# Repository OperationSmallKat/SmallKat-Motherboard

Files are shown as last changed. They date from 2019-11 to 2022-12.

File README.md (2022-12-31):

# Esp32-S3 Motherboard

## Pins
|Pin|Use|
|---|---|
| 0| Boot|
| 1| Servo 15|
| 2| Servo 14|
| 3| Servo 13|
| 4| Servo 12|
| 5| Fuse 4 ADC|
| 6| Fuse 1 ADC|
| 7| Servo 0|
| 8| Servo 1|
| 9| Servo 2|
| 10| Servo 3|
| 11| Fuse 2 ADC|
| 12| Servo 4|
| 13| Servo 5|
| 14| Servo 6|
| 15| 6V ADC|
| 16| Batt Voltage ADC|
| 17| Fuse 3 ADC|
| 18| Fuse 5 ADC|
| 19| USB -|
| 20| USB +|
| 21| Servo 7|
| 26| AD Servo 1|
| 33| AD Servo 3|
| 34| AD Servo 4|
| 35| Batt Serial TX|
| 36| Heart Beat LED|
| 37| Servo 8|
| 38| Servo 9|
| 39| Servo 10|
| 40| Servo 11|
| 41| SDA|
| 42| SCL|
| 43| TX|
| 44| RX|
| 45| |
| 46| |
| 47| AD Servo 2|
| 48| Batt Serial RX|

## I2C

  * i2c (SCL 42, SDA 41) - BNO055

## Serial 
  * Serial 0: Tx 43, Rx 44
  * Serial 1: Tx 35, Rx 48

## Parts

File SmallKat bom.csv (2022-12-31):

Comment | Designator | Footprint | Num | LCSC
BNO085 | AC1 | BNO085:BNO085 | 1 |  | 18.5 | 18.5
10pF | C15,C16 | Capacitor_SMD:C_0402_1005Metric | 2 | C313080 | 0.0009 | 0.0018
22uF | C17 | Capacitor_SMD:C_0805_2012Metric | 1 | C602037 | 0.0239 | 0.0239
0.1uF | C3,C12,C14,C18,C22,C23 | Capacitor_SMD:C_0402_1005Metric | 6 | C359190 | 0.0008 | 0.0048
2.2uF | C2,C5 | Capacitor_SMD:C_0805_2012Metric | 2 | C2176762 | 0.0076 | 0.0152
1000pF | C24 | Capacitor_SMD:C_0402_1005Metric | 1 | C696907 | 0.0006 | 0.0006
100pF | C25 | Capacitor_SMD:C_0402_1005Metric | 1 | C5142577 | 0.0007 | 0.0007
10nF | C26 | Capacitor_SMD:C_0402_1005Metric | 1 | C115654 | 0.0007 | 0.0007
1uF | C27,C36 | Capacitor_SMD:C_0402_1005Metric | 2 | C5137499 | 0.0021 | 0.0042
4.7uF | C28 | Capacitor_SMD:C_0402_1005Metric | 1 | C255498 | 0.0148 | 0.0148
470nF | C29 | Capacitor_SMD:C_0402_1005Metric | 1 | C2887019 | 0.0026 | 0.0026
10uF | C30,C32 | Capacitor_SMD:C_1206_3216Metric | 2 | C2174589 | 0.0183 | 0.0366
47uF | C31,C34 | Capacitor_SMD:C_1206_3216Metric | 2 | C172351 | 0.2142 | 0.4284
100uF | C33,C35 | Capacitor_SMD:C_1210_3225Metric | 2 | C90143 | 0.5998 | 1.1996
10uF | C4,C6 | Capacitor_SMD:C_0805_2012Metric | 2 | C3015161 | 0.009 | 0.018
LED | D1,D2,D3,D6,D9,D10,D11,D12,D13 | LED_SMD:LED_0603_1608Metric | 9 | C965799 | 0.0029 | 0.0261
DIODE | D4,D5 | Diode_SMD:D_SOD-123F | 2 | C5199128 | 0.0061 | 0.0122
D_TVS | D7,D8 | Diode_SMD:D_SOD-523 | 2 | C1974929 | 0.73 | 1.46
Fuse | F1,F2,F3,F4,F5 | 01550900M:0154.250DR | 5 | C108518 | 0.4837 | 2.4185
Fuse | F6,F7 | Fuse:Fuse_1206_3216Metric | 2 | C136343 | 0.0497 | 0.0994
LMR14010A | IC1,IC2 | Package_TO_SOT_SMD:SOT-23-6 | 2 | C388174 | 1.36 | 2.72
TPS40192DRCT-TPS40192DRCT | IC3 | Package_SON:VSON-10-1EP_3x3mm_P0.5mm_EP1.2x2mm | 1 | C3033463 | 0.1058 | 0.1058
ESP32-S3-MINI-1-N8 | IC4 | ESP32-s3-wroom-mini:ESP32S3MINI1N8 | 1 | C2913206 | 4.15 | 4.15
BATT_SERIAL | J1 | Connector_JST:JST_PH_B2B-PH-SM4-TB_1x02-1MP_P2.00mm_Vertical | 1 |  |  | 0
Conn_01x02_Female | J25 | RC-Battery-Connectors:XT-60_male | 1 | C99102 | 0.2323 | 0.2323
USB_C_Receptacle | J8 | C167321:C167321 | 1 | C167321 | 0.3369 | 0.3369
10uH | L1,L2 | Inductor_SMD:L_0805_2012Metric | 2 | C2991766 | 0.0715 | 0.143
1uH | L3 | Inductor_SMD:L_Bourns_SRP1245A | 1 | C3002722 | 0.3193 | 0.3193
BUK9M17-30EX / BUK7M10-40E | Q2,Q3 | Package_SON:VSON-8_3.3x3.3mm_P0.65mm_NexFET | 2 | C3033463 | 0.1058 | 0.2116
330R | R1,R16 | Resistor_SMD:R_0402_1005Metric | 2 | C105875 | 0.0004 | 0.0008
33.2 | R11,R12 | Resistor_SMD:R_0402_1005Metric | 2 | C130276 | 0.0005 | 0.001
5.1K | R14,R18 | Resistor_SMD:R_0402_1005Metric | 2 | C2906948 | 0.0004 | 0.0008
10K | R2,R4,R7,R10,R13,R15,R17,R19,R20,R23,R24,R27,R30,R33 | Resistor_SMD:R_0402_1005Metric | 14 | C25531 | 0.0004 | 0.0056
2.4K | R3 | Resistor_SMD:R_0402_1005Metric | 1 | C5140692 | 0.0004 | 0.0004
2.18k | R36 | Resistor_SMD:R_0402_1005Metric | 1 | C2906920 | 0.0004 | 0.0004
20k | R37 | Resistor_SMD:R_0402_1005Metric | 1 | C102876 | 0.0005 | 0.0005
2.61k | R38 | Resistor_SMD:R_0402_1005Metric | 1 | C170274 | 0.0008 | 0.0008
4.22k | R39 | Resistor_SMD:R_0402_1005Metric | 1 | C25898 | 0.0006 | 0.0006
12k | R40 | Resistor_SMD:R_0402_1005Metric | 1 | C100582 | 0.0004 | 0.0004
100k | R41,R42 | Resistor_SMD:R_0402_1005Metric | 2 | C2906883 | 0.0004 | 0.0008
1K | R43 | Resistor_SMD:R_0402_1005Metric | 1 | C100571 | 0.0004 | 0.0004
8.2K | R5,R8,R25,R28,R31,R34 | Resistor_SMD:R_0402_1005Metric | 6 | C2906967 | 0.0004 | 0.0024
120K | R6 | Resistor_SMD:R_0402_1005Metric | 1 | C2906887 | 0.0004 | 0.0004
20K | R9,R26,R29,R32,R35 | Resistor_SMD:R_0402_1005Metric | 5 | C102876 | 0.0005 | 0.0025
SW_SPST | SW1,SW2 | Button_Switch_SMD:SW_SPST_EVQPE1 | 2 | C410373 | 0.0443 | 0.0886
32.768kHz | Y1 | Crystal:Crystal_SMD_2012-2Pin_2.0x1.2mm | 1 | C96341 | 0.2301 | 0.2301
Conn_01x03_Male | J3,J4,J5,J6,J9,J10,J11,J12,J13,J14,J15,J16,J17,J18,J19,J20,J21,J22,J23,J24 | Connector_PinHeader_2.54mm:PinHeader_1x03_P2.54mm_Vertical | 20 | C5333416 | 0.0469 | 0.938
 |  |  |  |  |  | 33.7615

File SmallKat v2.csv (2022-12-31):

Comment | Designator | Footprint | LCSC
BNO085 | AC1 | BNO085:BNO085
10pF | C15,C16 | Capacitor_SMD:C_0402_1005Metric
22uF | C17 | Capacitor_SMD:C_0805_2012Metric
0.1uF | C3,C12,C14,C18,C22,C23 | Capacitor_SMD:C_0402_1005Metric
2.2uF | C2,C5 | Capacitor_SMD:C_0805_2012Metric
1000pF | C24 | Capacitor_SMD:C_0402_1005Metric
100pF | C25 | Capacitor_SMD:C_0402_1005Metric
10nF | C26 | Capacitor_SMD:C_0402_1005Metric
1uF | C27,C36 | Capacitor_SMD:C_0402_1005Metric
4.7uF | C28 | Capacitor_SMD:C_0402_1005Metric
470nF | C29 | Capacitor_SMD:C_0402_1005Metric
10uF | C30,C32 | Capacitor_SMD:C_1206_3216Metric
47uF | C31,C34 | Capacitor_SMD:C_1206_3216Metric
100uF | C33,C35 | Capacitor_SMD:C_1210_3225Metric
10uF | C4,C6 | Capacitor_SMD:C_0805_2012Metric
LED | D1,D2,D3,D6,D9,D10,D11,D12,D13 | LED_SMD:LED_0603_1608Metric
DIODE | D4,D5 | Diode_SMD:D_SOD-123F
D_TVS | D7,D8 | Diode_SMD:D_SOD-523
Fuse | F1,F2,F3,F4,F5 | 01550900M:0154.250DR
Fuse | F6,F7 | Fuse:Fuse_1206_3216Metric
MountingHole_Pad | H1,H2,H3,H4 | MountingHole:MountingHole_3.2mm_M3_Pad_Via
LMR14010A | IC1,IC2 | Package_TO_SOT_SMD:SOT-23-6
TPS40192DRCT-TPS40192DRCT | IC3 | Package_SON:VSON-10-1EP_3x3mm_P0.5mm_EP1.2x2mm
ESP32-S3-MINI-1-N8 | IC4 | ESP32-s3-wroom-mini:ESP32S3MINI1N8
BATT_SERIAL | J1 | Connector_JST:JST_PH_B2B-PH-SM4-TB_1x02-1MP_P2.00mm_Vertical
Conn_01x02_Female | J25 | RC-Battery-Connectors:XT-60_male
Conn_01x03_Male | J3,J4,J5,J6,J9,J10,J11,J12,J13,J14,J15,J16,J17,J18,J19,J20,J21,J22,J23,J24 | Connector_PinHeader_2.54mm:PinHeader_1x03_P2.54mm_Vertical
USB_C_Receptacle | J8 | C167321:C167321
10uH | L1,L2 | Inductor_SMD:L_0805_2012Metric
1uH | L3 | Inductor_SMD:L_Bourns_SRP1245A
BUK9M17-30EX / BUK7M10-40E | Q2,Q3 | Package_SON:VSON-8_3.3x3.3mm_P0.65mm_NexFET
330R | R1,R16 | Resistor_SMD:R_0402_1005Metric
33.2 | R11,R12 | Resistor_SMD:R_0402_1005Metric
5.1K | R14,R18 | Resistor_SMD:R_0402_1005Metric
10K | R2,R4,R7,R10,R13,R15,R17,R19,R20,R23,R24,R27,R30,R33 | Resistor_SMD:R_0402_1005Metric
2.4K | R3 | Resistor_SMD:R_0402_1005Metric
2.18k | R36 | Resistor_SMD:R_0402_1005Metric
20k | R37 | Resistor_SMD:R_0402_1005Metric
2.61k | R38 | Resistor_SMD:R_0402_1005Metric
4.22k | R39 | Resistor_SMD:R_0402_1005Metric
12k | R40 | Resistor_SMD:R_0402_1005Metric
100k | R41,R42 | Resistor_SMD:R_0402_1005Metric
1K | R43 | Resistor_SMD:R_0402_1005Metric
8.2K | R5,R8,R25,R28,R31,R34 | Resistor_SMD:R_0402_1005Metric
120K | R6 | Resistor_SMD:R_0402_1005Metric
20K | R9,R26,R29,R32,R35 | Resistor_SMD:R_0402_1005Metric
SW_SPST | SW1,SW2 | Button_Switch_SMD:SW_SPST_EVQPE1
Check for life | TP1 | TestPoint:TestPoint_Pad_D2.0mm
GND | TP10 | TestPoint:TestPoint_Pad_D2.0mm
6V | TP11 | TestPoint:TestPoint_Pad_D2.0mm
SDA | TP2 | TestPoint:TestPoint_Pad_D2.0mm
SCL | TP3 | TestPoint:TestPoint_Pad_D2.0mm
3.3v | TP4 | TestPoint:TestPoint_Pad_D2.0mm
TestPoint | TP5,TP6,TP7,TP14,TP15 | TestPoint:TestPoint_Pad_D2.0mm
Batt+ | TP9 | TestPoint:TestPoint_Pad_D2.0mm
32.768kHz | Y1 | Crystal:Crystal_SMD_2012-2Pin_2.0x1.2mm

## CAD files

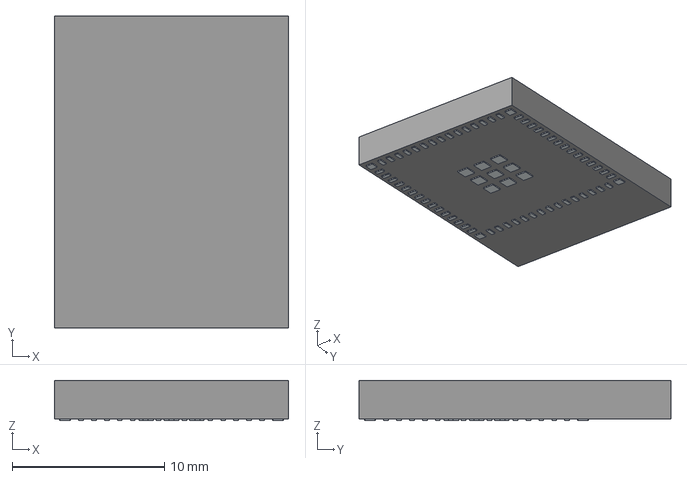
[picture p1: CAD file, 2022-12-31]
3D_models/ESP32-S3-MINI-1-N8.stp
15.4 x 20.5 x 2.65 mm
Pins

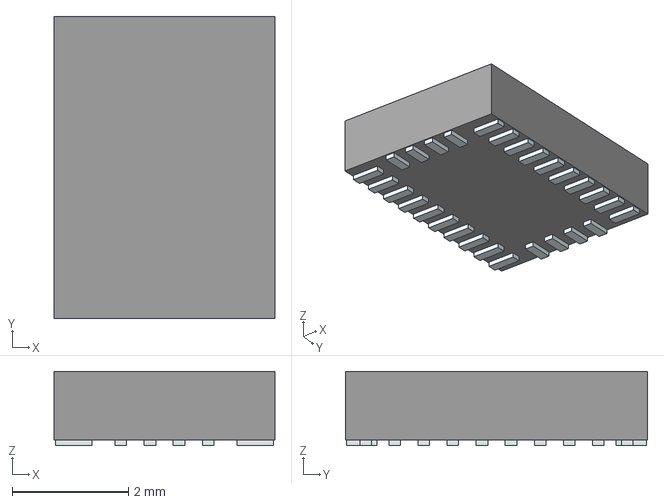
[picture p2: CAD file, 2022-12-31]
BNO085/BNO085.stp
3.80 x 5.20 x 1.28 mm
Pins

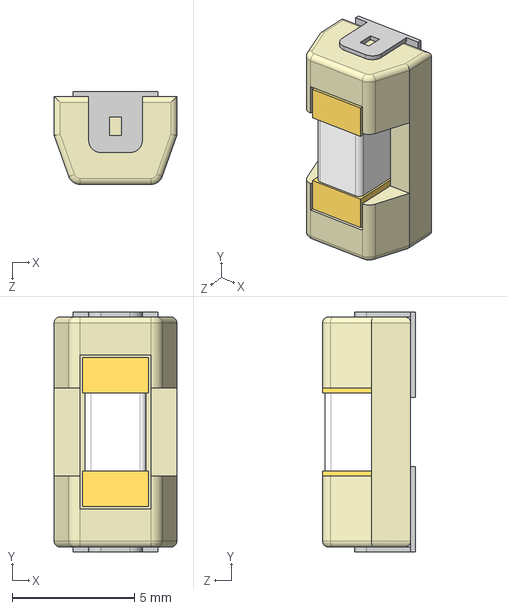
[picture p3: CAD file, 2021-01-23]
3D_models/User Library-OMNI-BLOK littelfuse.STEP
5.03 x 9.83 x 3.81 mm

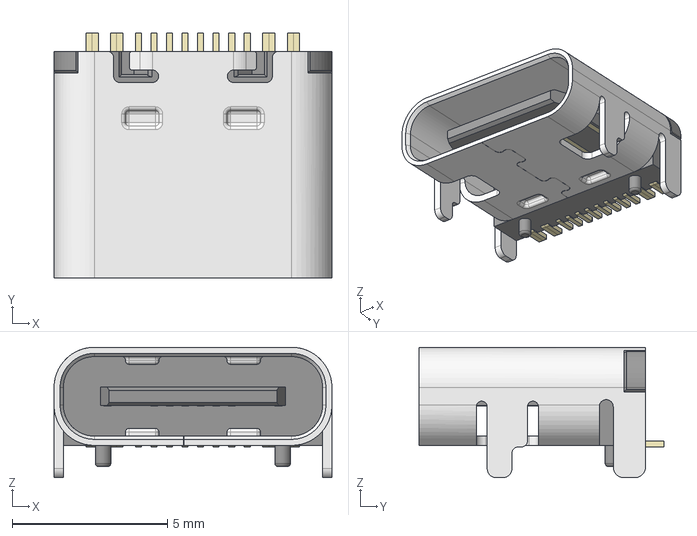
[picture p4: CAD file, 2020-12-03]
3D_models/HRO_TYPE-C-31-M-12.step
8.95 x 7.90 x 4.20 mm

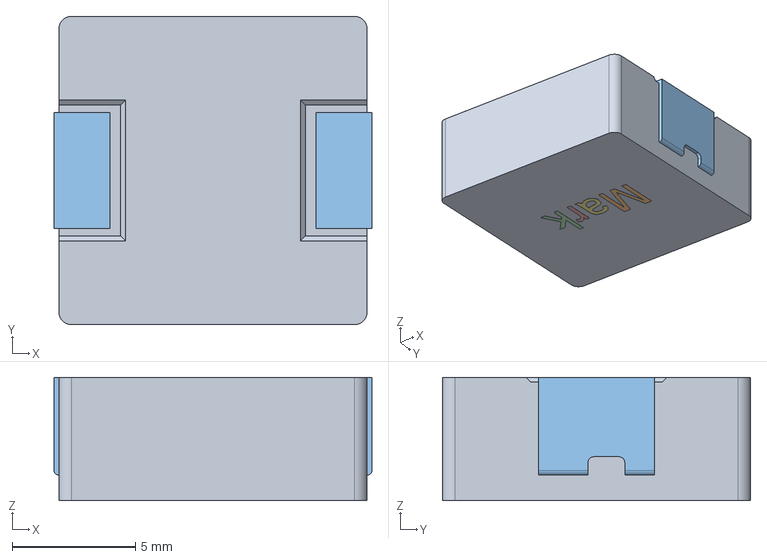
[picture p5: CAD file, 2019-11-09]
3D_models/SRP1245A series.stp
12.9 x 12.5 x 5.00 mm

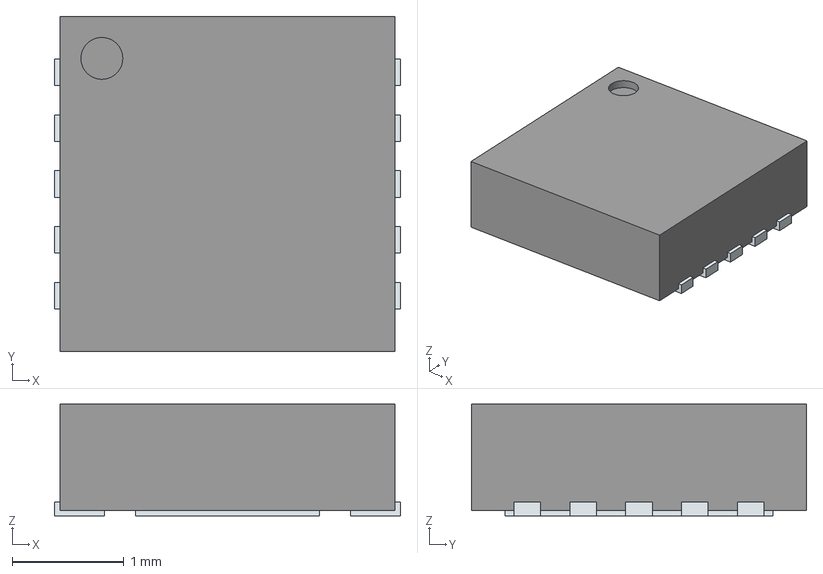
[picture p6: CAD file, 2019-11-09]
TPS40192/TPS40192DRCT.stp
3.10 x 3.00 x 1.00 mm
ThermalPin
PinsArrayLR

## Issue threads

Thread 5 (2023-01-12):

Things to address in S3 board rev version

keionbis, 2023-01-12:
This is a list of things to address in the current version of the S3 board, things found after testing and to decide if we can have JLC do a full board assembly
- [x] Source Inductor from JLCPCB components
> - [x]  Update footprint to match decided Inductor
- [x] Source fets from JLCPCB components (Double check footprint and RDS on to make sure current lim is good)
> - [x]  Update footprint to match decided fets
- [x] Source Battery Serial connector from JLCPCB components
> - [x]  Update footprint to match decided connector
- [x] Source pin headers for servo from JLCPCB components
- [ ] RFQ BNO055 from JLC
- [x] Source Buttons from JLCPCB components
> - [x]  Update footprint to match decided button
- [x] Source fuse holder with 5A fuses installed from JLCPCB components
- [x] Change SCL and SDA pins from 45, 46
- [x] Source correct TVS diodes form JLCPCB components
> - [x] Correct TVS diode footprints
- [ ] #6
- [x] Verify cap on GPIO0
- [x]  Source XT30 from JLCPCB components
> - [x] Verify pin 1 matches on board and manufacturer definition
- [x] Fix short between fet output and VBUS
- [ ] #9

keionbis, 2023-01-13:
To get the correct short circuit current and current lim on the switchmode PSU, the 12K ohm resistor (R40) on the comp pin is left unpopulated

keionbis, 2023-01-13:
Button: Korean Hroparts Elec K2-1107ST-A4SW-06
Batt serial connector: MOLEX 0533980271
XT30: Changzhou Amass Elec XT30U-M
TVS Diode: LRC LESD5D5.0CT1G
Fuse holder with fuse: Littelfuse 0154005.DRT
tht pin headers: BOOMELE(Boom Precision Elec) C49257
Fets: Alpha & Omega Semicon AON7262E
Inductor: cjiang(Changjiang Microelectronics Tech) FXC1265-1R0M

Closed 2023-01-13.

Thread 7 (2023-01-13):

Things to test on S3 model

keionbis, 2023-01-13:
- [x] Programming
- [x] IMU
- [x] PWMs
- [x] 6V
- [x] 3V
- [x] Battery Serial pins
- [x] ADCs
- [x] 6V sense

keionbis, 2023-01-13:
All have been tested and are working. The only issues were i2c should be moved off of pin 45, 46 and output of the 6v fets is shorted to vbus. These are tracked in #5

Closed 2023-01-13.

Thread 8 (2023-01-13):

Add 3.3v+ gnd connector towards head for expansion board

keionbis, 2023-01-13:
@madhephaestus wants to be able add on secondary esp32 board in the head, this needs power and should, should only need a connector for 3.3v and gnd.

This can use the same molex pico blade connector from the battery serial

madhephaestus, 2023-01-13:
do you have a suggestion of a good module for this?

keionbis, 2023-01-13:
depends what you actally want from it, If its just a camera it would be something like the espeye or a derivative board. If you want other things like an imu then we would probably need to spin up a board for it

madhephaestus, 2023-01-13:
yeah, ok. This one? https://www.mouser.com/ProductDetail/Espressif-Systems/ESP-EYE?qs=l7cgNqFNU1iWrlpTZmwCRA%3D%3D

keionbis, 2023-01-13:
Might be worth using this one instead https://www.mouser.com/ProductDetail/M5Stack/U082?qs=81r%252BiQLm7BTFg2IRCU1YKQ%3D%3D
It gives us a convenient place to give it 3.3v with the connector at the bottom

madhephaestus, 2023-01-13:
ok, cool

keionbis, 2023-03-13:
added in the newest board rev

Closed 2023-03-13.

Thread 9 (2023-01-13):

Decide of we need 4 layer boards or if 2 is enough

keionbis, 2023-01-13:

keionbis, 2023-01-13:
price difference for 50 boards is $21 for 2 layer boards vs $59 for 4 layer. This equates to a $0.76 price increase per board. However in testing there was no significant decrease in power carrying capabilities for 6v.

keionbis, 2023-06-13:
2 layers is enough at least for this rev

Closed 2023-06-13.

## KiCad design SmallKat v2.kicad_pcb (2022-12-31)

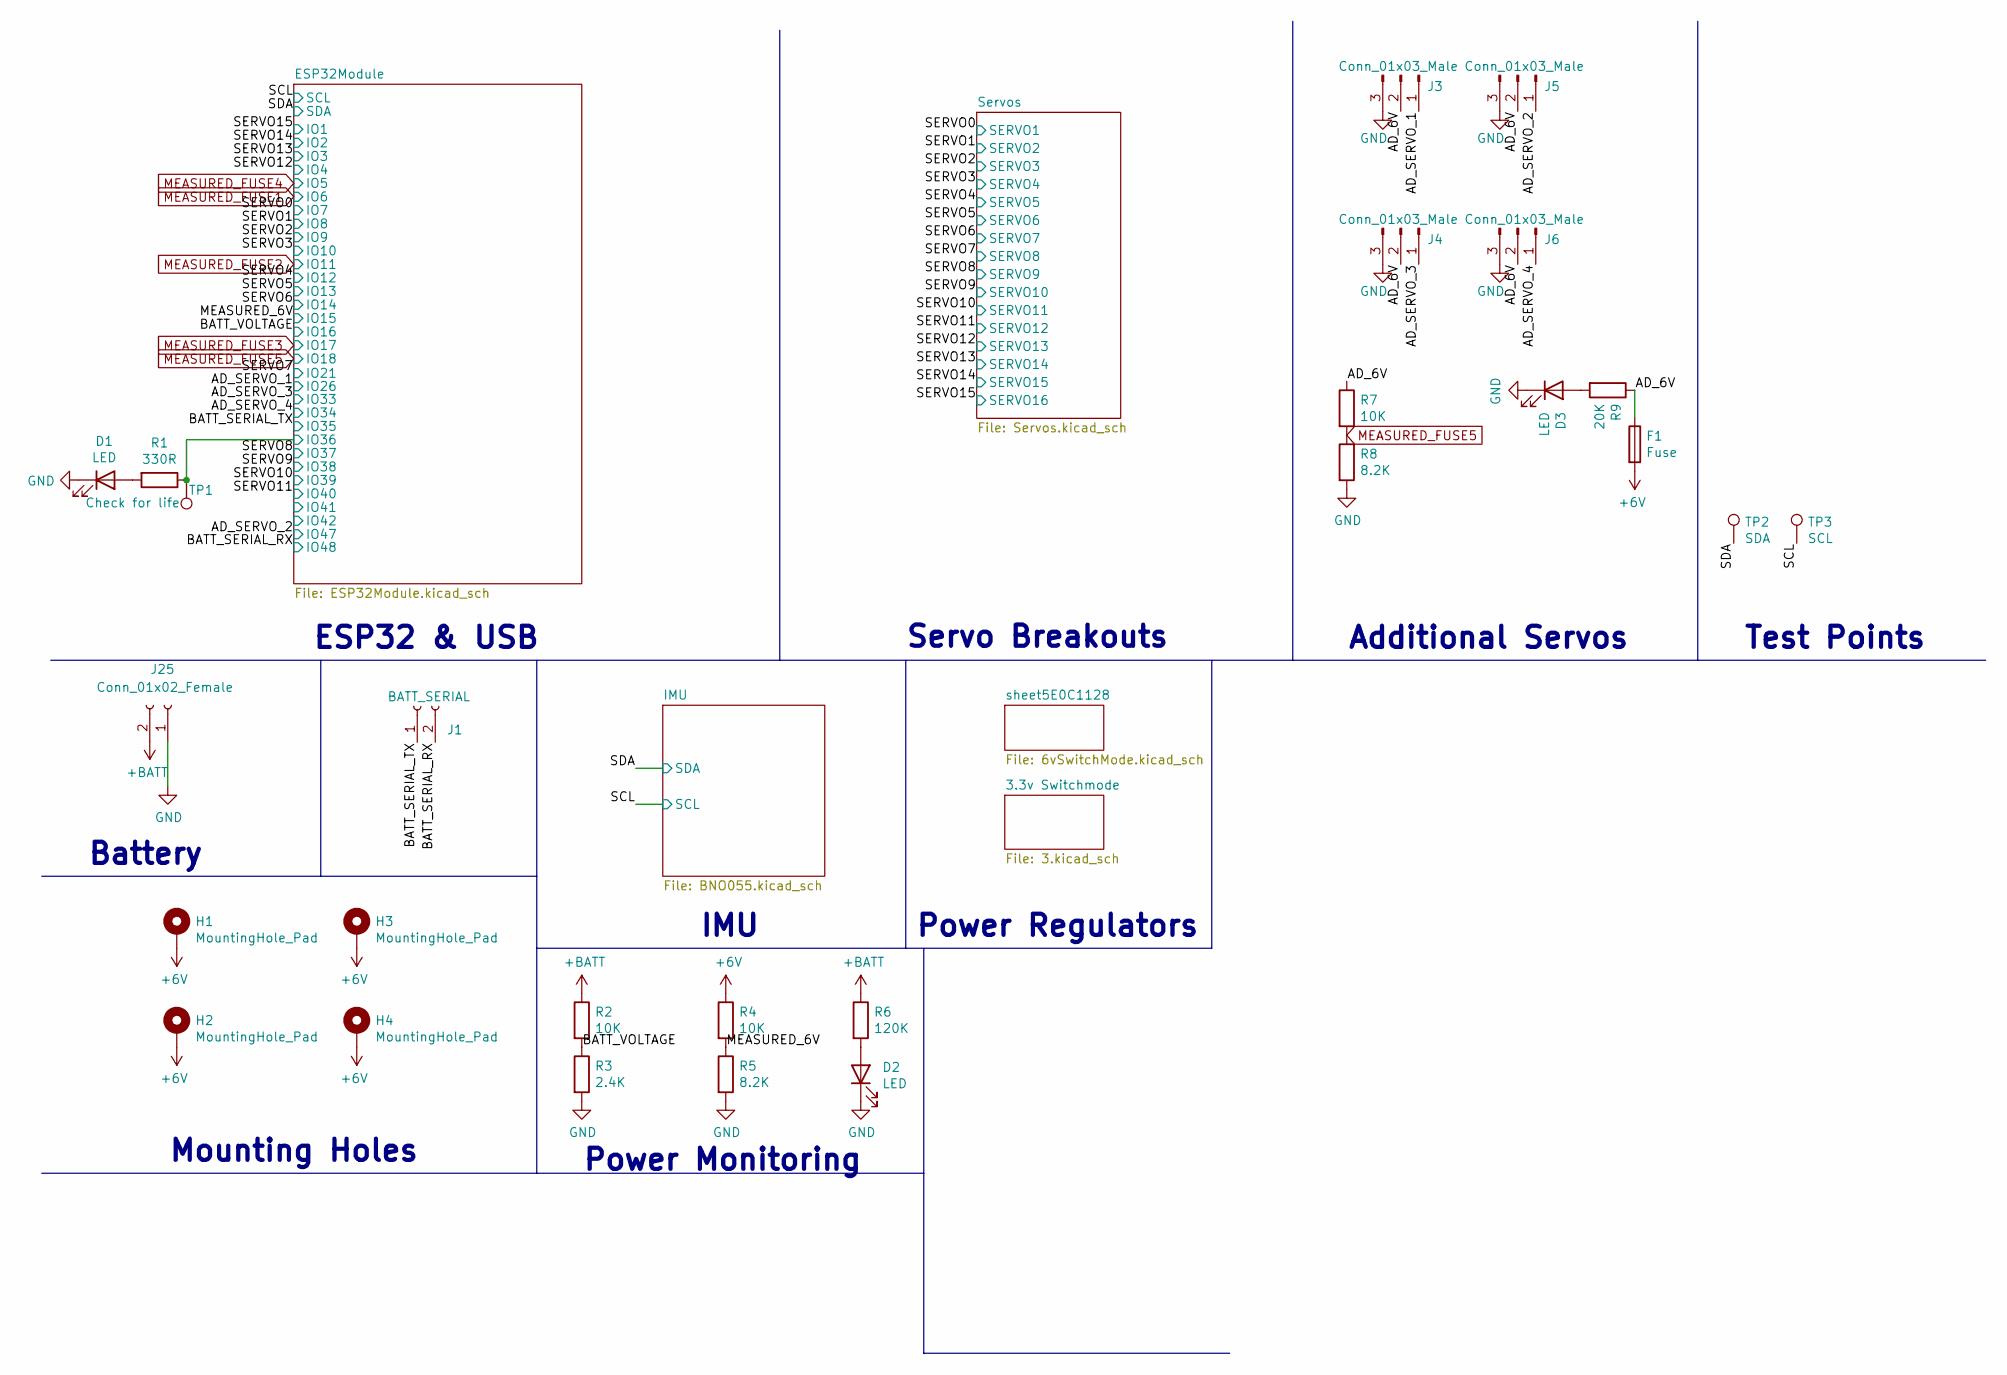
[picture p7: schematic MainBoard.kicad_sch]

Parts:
D1, D2, D3: LED; LED_0603_1608Metric
F1: Fuse; 0154.250DR
H1, H2, H3, H4: MountingHole_Pad; MountingHole_3.2mm_M3_Pad_Via
J1: BATT_SERIAL; JST_PH_B2B-PH-SM4-TB_1x02-1MP_P2.00mm_Vertical
J3, J4, J5, J6: Conn_01x03_Male; PinHeader_1x03_P2.54mm_Vertical
J25: Conn_01x02_Female; XT-60_male
R1: 330R; R_0402_1005Metric
R2, R4, R7: 10K; R_0402_1005Metric
R3: 2.4K; R_0402_1005Metric
R5, R8: 8.2K; R_0402_1005Metric
R6: 120K; R_0402_1005Metric
R9: 20K; R_0402_1005Metric
TP1: Check for life; TestPoint_Pad_D2.0mm
TP2: SDA; TestPoint_Pad_D2.0mm
TP3: SCL; TestPoint_Pad_D2.0mm

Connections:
+6V: F1.2, H1.1, H2.1, H3.1, H4.1, R4.1; also elsewhere on the board
+BATT: J25.2, R2.1, R6.1; also elsewhere on the board
/MainBoard/AD_6V: F1.1, J3.2, J4.2, J5.2, J6.2, R7.1, R9.1
/MainBoard/AD_SERVO_1: J3.1; also elsewhere on the board
/MainBoard/AD_SERVO_2: J5.1; also elsewhere on the board
/MainBoard/AD_SERVO_3: J4.1; also elsewhere on the board
/MainBoard/AD_SERVO_4: J6.1; also elsewhere on the board
/MainBoard/BATT_SERIAL_RX: J1.2; also elsewhere on the board
/MainBoard/BATT_SERIAL_TX: J1.1; also elsewhere on the board
/MainBoard/BATT_VOLTAGE: R2.2, R3.1; also elsewhere on the board
/MainBoard/ESP32Module/IO36: R1.1, TP1.1; also elsewhere on the board
/MainBoard/MEASURED_6V: R4.2, R5.1; also elsewhere on the board
/MainBoard/SCL: TP3.1; also elsewhere on the board
/MainBoard/SDA: TP2.1; also elsewhere on the board
GND: D1.1 (K), D2.1 (K), D3.1 (K), J3.3, J4.3, J5.3, J6.3, J25.1, R3.2, R5.2, R8.2; also elsewhere on the board
MEASURED_FUSE5: R7.2, R8.1; also elsewhere on the board
unnamed: D1.2 (A), R1.2
unnamed: D2.2 (A), R6.2
unnamed: D3.2 (A), R9.2

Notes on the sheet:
IMU
Test Points
ESP32 & USB
Power Regulators
Additional Servos
Battery
Power Monitoring
Mounting Holes
Servo Breakouts

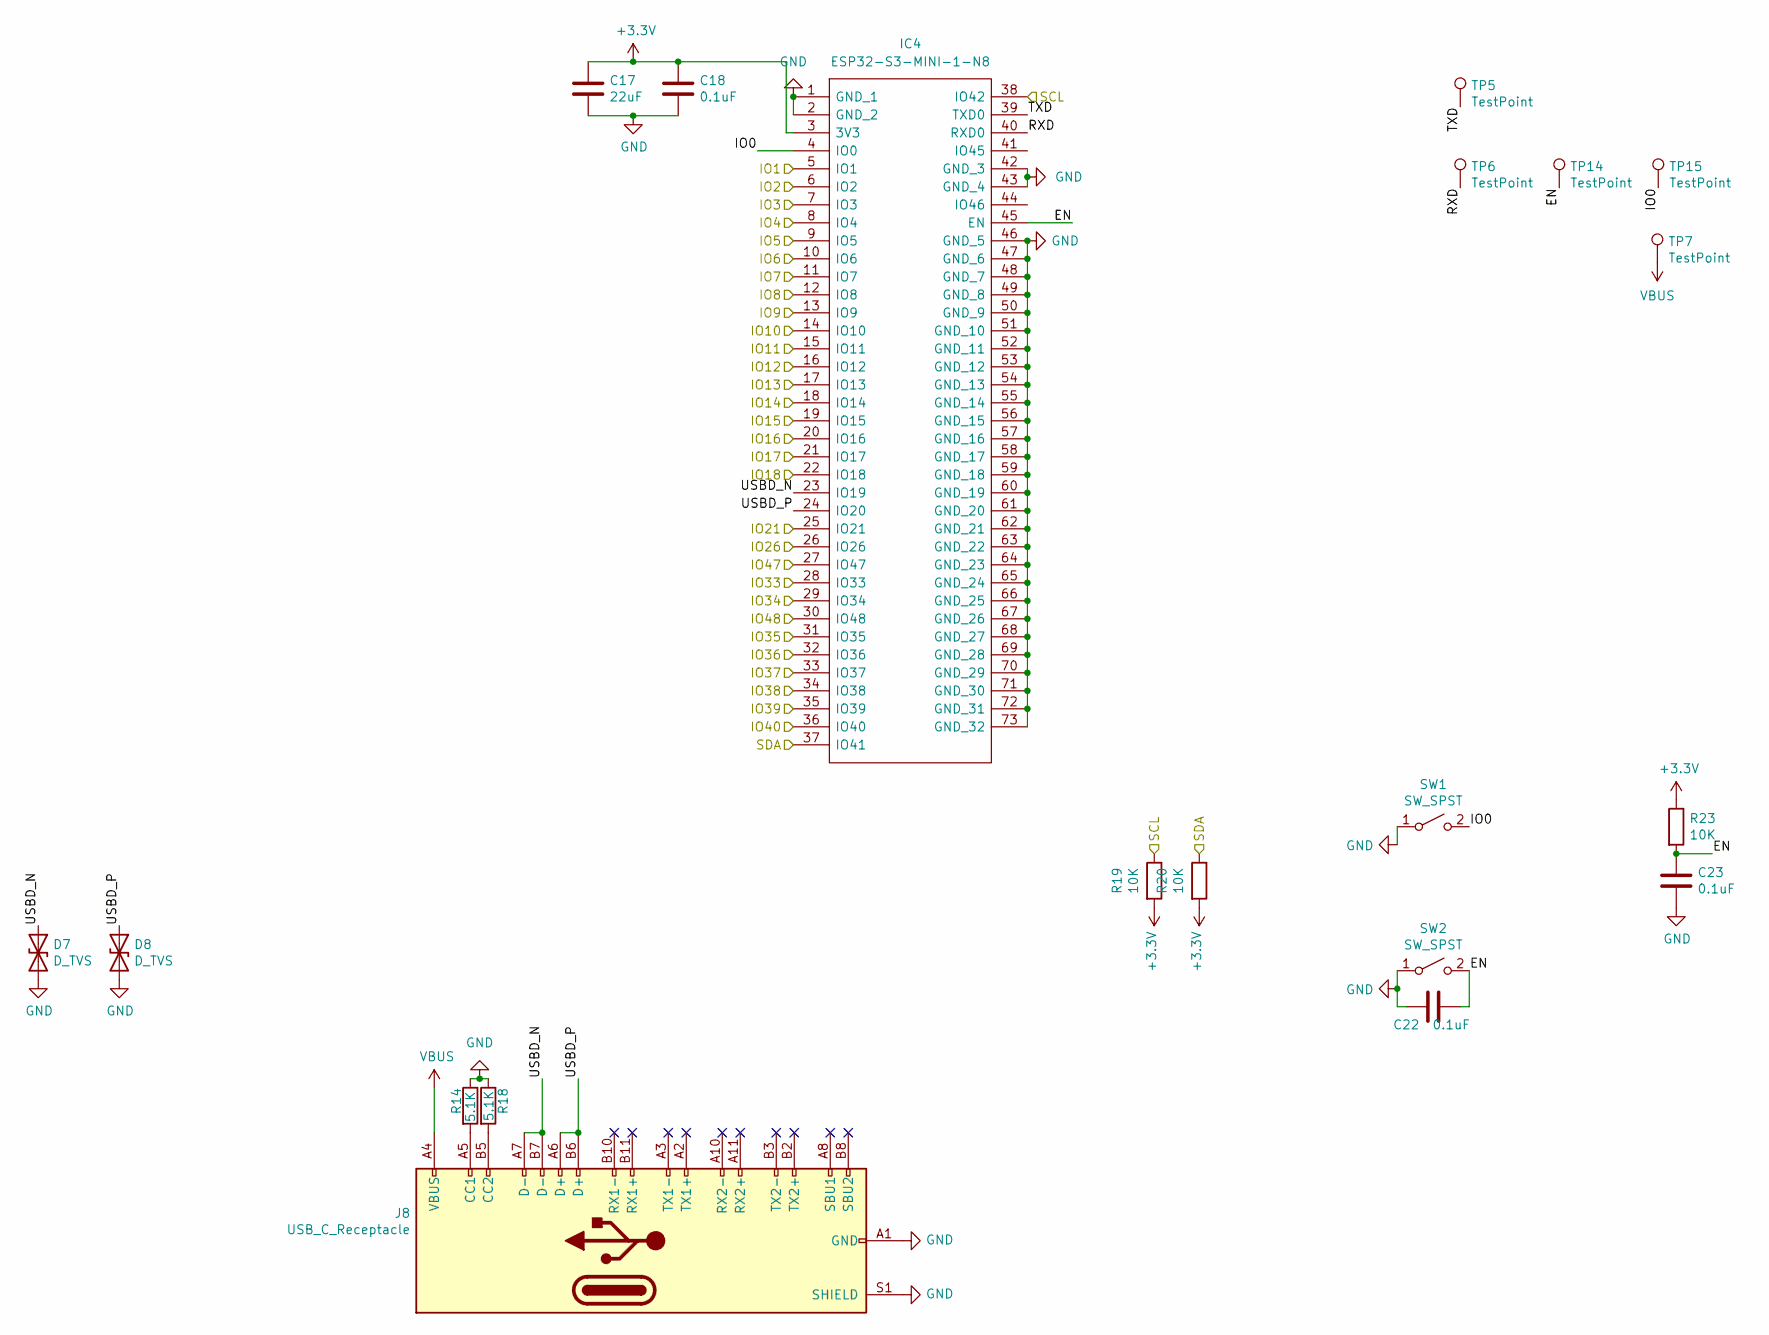
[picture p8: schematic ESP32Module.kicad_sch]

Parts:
C17: 22uF; C_0805_2012Metric
C18, C22, C23: 0.1uF; C_0402_1005Metric
D7, D8: D_TVS; D_SOD-523
IC4: ESP32-S3-MINI-1-N8; ESP32S3MINI1N8; Manufacturer_Part_Number ESP32-S3-MINI-1-N8; Mouser Part Number 356-ESP32-S3-MINI1N8
J8: USB_C_Receptacle; C167321
R14, R18: 5.1K; R_0402_1005Metric
R19, R20, R23: 10K; R_0402_1005Metric
SW1, SW2: SW_SPST; SW_SPST_EVQPE1
TP5, TP6, TP7, TP14, TP15: TestPoint; TestPoint_Pad_D2.0mm

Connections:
/MainBoard/AD_SERVO_1: IC4.26 (IO26); also elsewhere on the board
/MainBoard/AD_SERVO_2: IC4.27 (IO47); also elsewhere on the board
/MainBoard/AD_SERVO_3: IC4.28 (IO33); also elsewhere on the board
/MainBoard/AD_SERVO_4: IC4.29 (IO34); also elsewhere on the board
/MainBoard/BATT_SERIAL_RX: IC4.30 (IO48); also elsewhere on the board
/MainBoard/BATT_SERIAL_TX: IC4.31 (IO35); also elsewhere on the board
/MainBoard/BATT_VOLTAGE: IC4.20 (IO16); also elsewhere on the board
/MainBoard/ESP32Module/EN: C22.1, C23.1, IC4.45 (EN), R23.2, SW2.2 (B), TP14.1
/MainBoard/ESP32Module/IO0: IC4.4 (IO0), SW1.2 (B), TP15.1
/MainBoard/ESP32Module/IO36: IC4.32 (IO36); also elsewhere on the board
/MainBoard/ESP32Module/RXD: IC4.40 (RXD0), TP6.1
/MainBoard/ESP32Module/TXD: IC4.39 (TXD0), TP5.1
/MainBoard/ESP32Module/USBD_N: D7.1 (A1), IC4.23 (IO19), J8.A7 (D-), J8.B7 (D-)
/MainBoard/ESP32Module/USBD_P: D8.1 (A1), IC4.24 (IO20), J8.A6 (D+), J8.B6 (D+)
/MainBoard/MEASURED_6V: IC4.19 (IO15); also elsewhere on the board
/MainBoard/SCL: IC4.38 (IO42), R19.1; also elsewhere on the board
/MainBoard/SDA: IC4.37 (IO41), R20.1; also elsewhere on the board
/MainBoard/SERVO0: IC4.11 (IO7); also elsewhere on the board
/MainBoard/SERVO1: IC4.12 (IO8); also elsewhere on the board
/MainBoard/SERVO2: IC4.13 (IO9); also elsewhere on the board
/MainBoard/SERVO3: IC4.14 (IO10); also elsewhere on the board
/MainBoard/SERVO4: IC4.16 (IO12); also elsewhere on the board
/MainBoard/SERVO5: IC4.17 (IO13); also elsewhere on the board
/MainBoard/SERVO6: IC4.18 (IO14); also elsewhere on the board
/MainBoard/SERVO7: IC4.25 (IO21); also elsewhere on the board
/MainBoard/SERVO8: IC4.33 (IO37); also elsewhere on the board
/MainBoard/SERVO9: IC4.34 (IO38); also elsewhere on the board
/MainBoard/SERVO10: IC4.35 (IO39); also elsewhere on the board
/MainBoard/SERVO11: IC4.36 (IO40); also elsewhere on the board
/MainBoard/SERVO12: IC4.8 (IO4); also elsewhere on the board
/MainBoard/SERVO13: IC4.7 (IO3); also elsewhere on the board
/MainBoard/SERVO14: IC4.6 (IO2); also elsewhere on the board
/MainBoard/SERVO15: IC4.5 (IO1); also elsewhere on the board
GND: C17.2, C18.2, C22.2, C23.2, D7.2 (A2), D8.2 (A2), IC4.1 (GND_1), IC4.2 (GND_2), IC4.42 (GND_3), IC4.43 (GND_4), IC4.46 (GND_5), IC4.47 (GND_6), IC4.48 (GND_7), IC4.49 (GND_8), IC4.50 (GND_9), IC4.51 (GND_10), IC4.52 (GND_11), IC4.53 (GND_12), IC4.54 (GND_13), IC4.55 (GND_14), IC4.56 (GND_15), IC4.57 (GND_16), IC4.58 (GND_17), IC4.59 (GND_18), IC4.60 (GND_19), IC4.61 (GND_20), IC4.62 (GND_21), IC4.63 (GND_22), IC4.64 (GND_23), IC4.65 (GND_24), IC4.66 (GND_25), IC4.67 (GND_26), IC4.68 (GND_27), IC4.69 (GND_28), IC4.70 (GND_29), IC4.71 (GND_30), IC4.72 (GND_31), IC4.73 (GND_32), J8.A1 (GND), J8.A12 (GND), J8.B1 (GND), J8.B12 (GND), J8.S1 (SHIELD), R14.1, R18.1, SW1.1 (A), SW2.1 (A); also elsewhere on the board
MEASURED_FUSE1: IC4.10 (IO6); also elsewhere on the board
MEASURED_FUSE2: IC4.15 (IO11); also elsewhere on the board
MEASURED_FUSE3: IC4.21 (IO17); also elsewhere on the board
MEASURED_FUSE4: IC4.9 (IO5); also elsewhere on the board
MEASURED_FUSE5: IC4.22 (IO18); also elsewhere on the board
unnamed: J8.A5 (CC1), R14.2
unnamed: J8.B5 (CC2), R18.2
VBUS: J8.A4 (VBUS), J8.A9 (VBUS), J8.B4 (VBUS), J8.B9 (VBUS), TP7.1; also elsewhere on the board

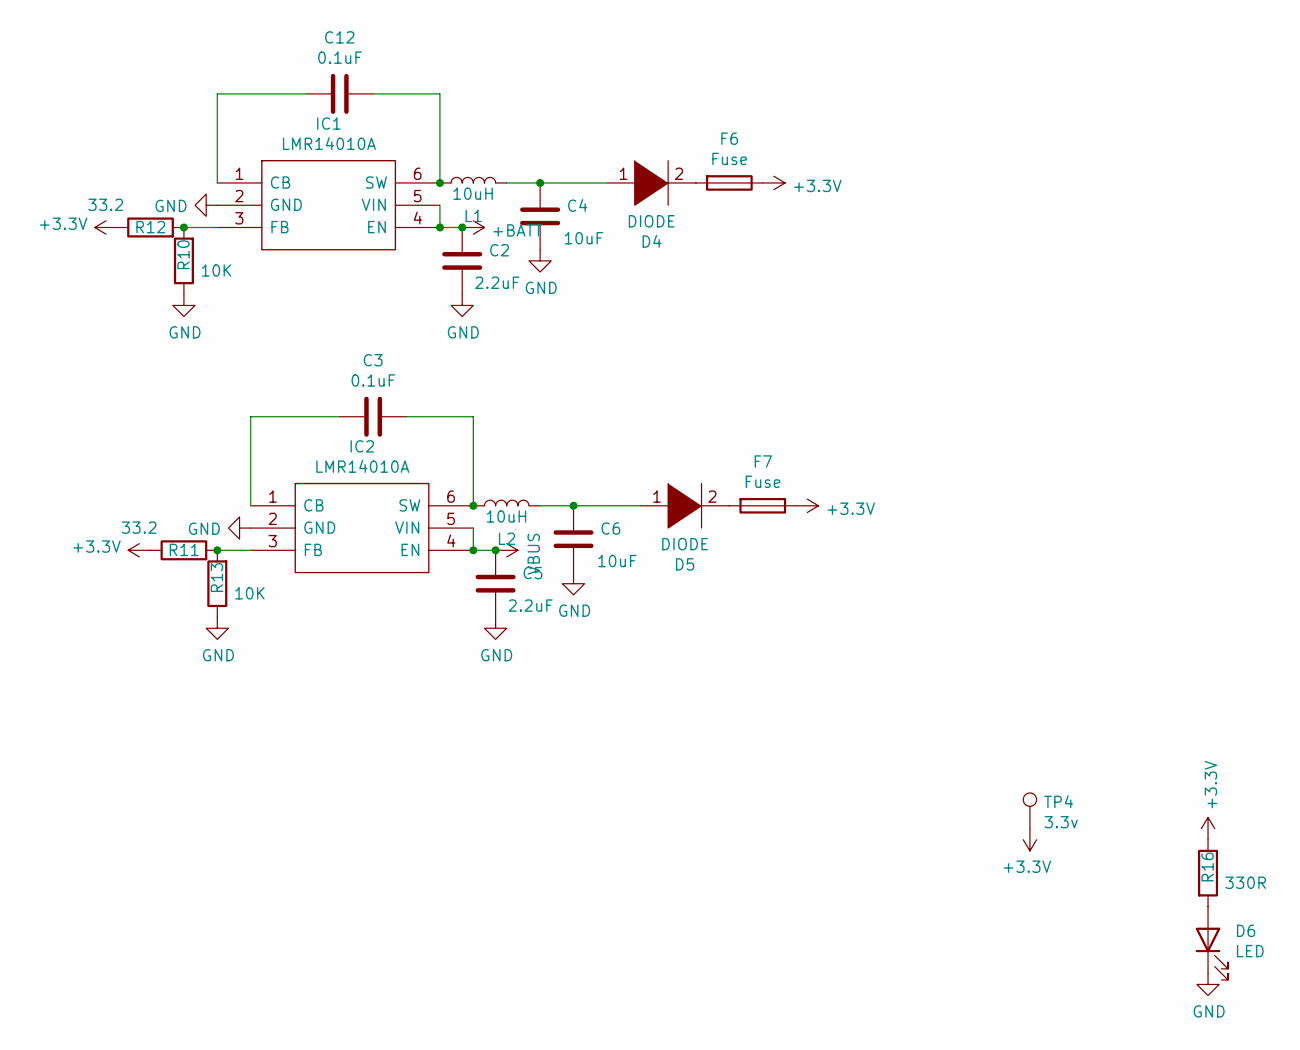
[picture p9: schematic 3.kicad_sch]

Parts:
C2, C5: 2.2uF; C_0805_2012Metric
C3, C12: 0.1uF; C_0402_1005Metric
C4, C6: 10uF; C_0805_2012Metric
D4, D5: DIODE; D_SOD-123F
D6: LED; LED_0603_1608Metric
F6, F7: Fuse; Fuse_1206_3216Metric
IC1, IC2: LMR14010A; SOT-23-6; Manufacturer_Part_Number LMR50410YQDBVRQ1; Mouser Part Number 595-LMR50410YQDBVRQ1
L1, L2: 10uH; L_0805_2012Metric
R10, R13: 10K; R_0402_1005Metric
R11, R12: 33.2; R_0402_1005Metric
R16: 330R; R_0402_1005Metric
TP4: 3.3v; TestPoint_Pad_D2.0mm

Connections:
+BATT: C2.1, IC1.4 (EN), IC1.5 (VIN); also elsewhere on the board
GND: C2.2, C4.2, C5.2, C6.2, D6.1 (K), IC1.2 (GND), IC2.2 (GND), R10.1, R13.1; also elsewhere on the board
unnamed: C3.1, IC2.6 (SW), L2.1
unnamed: C3.2, IC2.1 (CB)
unnamed: C4.1, D4.1 (K), L1.2
unnamed: C6.1, D5.1 (K), L2.2
unnamed: C12.1, IC1.6 (SW), L1.1
unnamed: C12.2, IC1.1 (CB)
unnamed: D4.2 (A), F6.2
unnamed: D5.2 (A), F7.2
unnamed: D6.2 (A), R16.2
unnamed: IC1.3 (FB), R10.2, R12.2
unnamed: IC2.3 (FB), R11.2, R13.2
VBUS: C5.1, IC2.4 (EN), IC2.5 (VIN); also elsewhere on the board

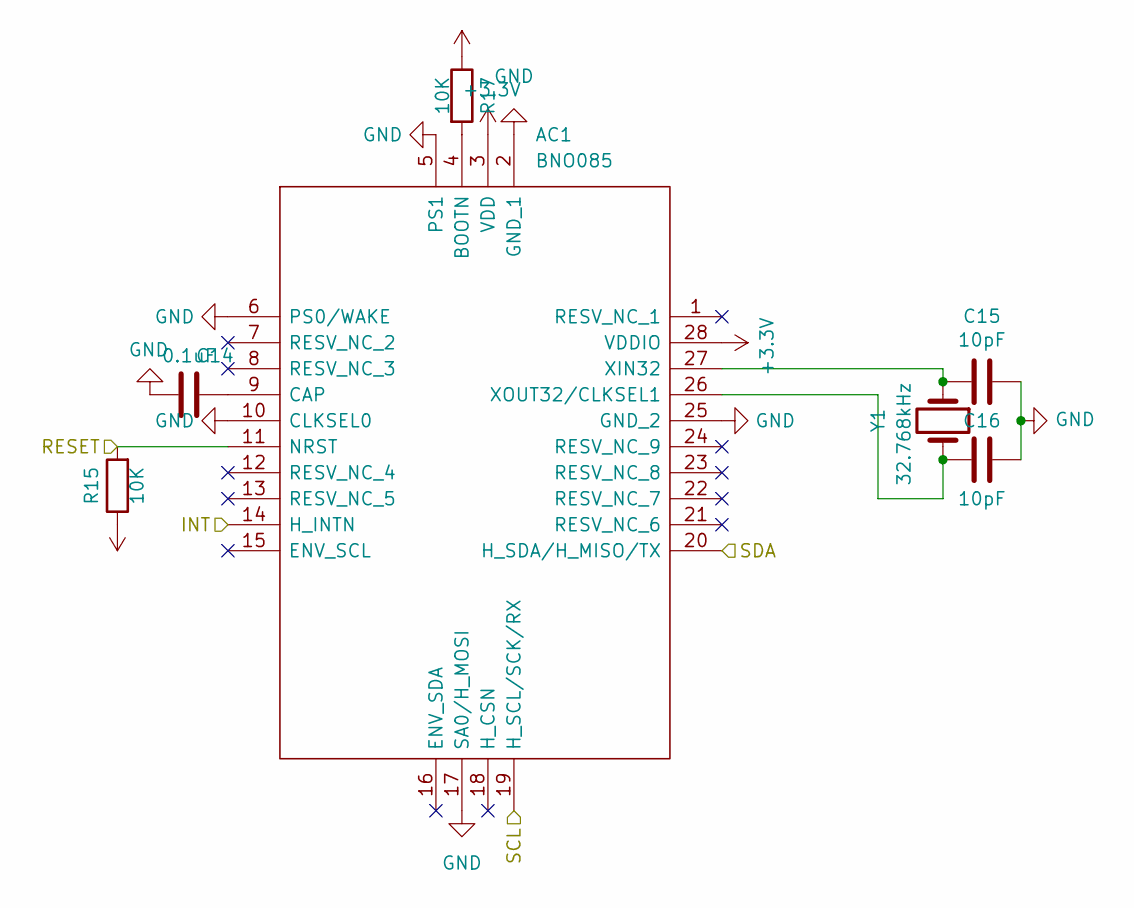
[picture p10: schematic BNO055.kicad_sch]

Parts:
AC1: BNO085; Manufacturer_Part_Number BNO085
C14: 0.1uF; C_0402_1005Metric
C15, C16: 10pF; C_0402_1005Metric
R15, R17: 10K; R_0402_1005Metric
Y1: 32.768kHz; Crystal_SMD_2012-2Pin_2.0x1.2mm

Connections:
/MainBoard/IMU/INT: AC1.14 (H_INTN)
/MainBoard/IMU/RESET: AC1.11 (NRST), R15.2
/MainBoard/SCL: AC1.19 (H_SCL/SCK/RX); also elsewhere on the board
/MainBoard/SDA: AC1.20 (H_SDA/H_MISO/TX); also elsewhere on the board
GND: AC1.2 (GND_1), AC1.5 (PS1), AC1.6 (PS0/WAKE), AC1.10 (CLKSEL0), AC1.17 (SA0/H_MOSI), AC1.25 (GND_2), C14.1, C15.1, C16.1; also elsewhere on the board
unnamed: AC1.4 (BOOTN), R17.2
unnamed: AC1.9 (CAP), C14.2
unnamed: AC1.26 (XOUT32/CLKSEL1), C16.2, Y1.2
unnamed: AC1.27 (XIN32), C15.2, Y1.1

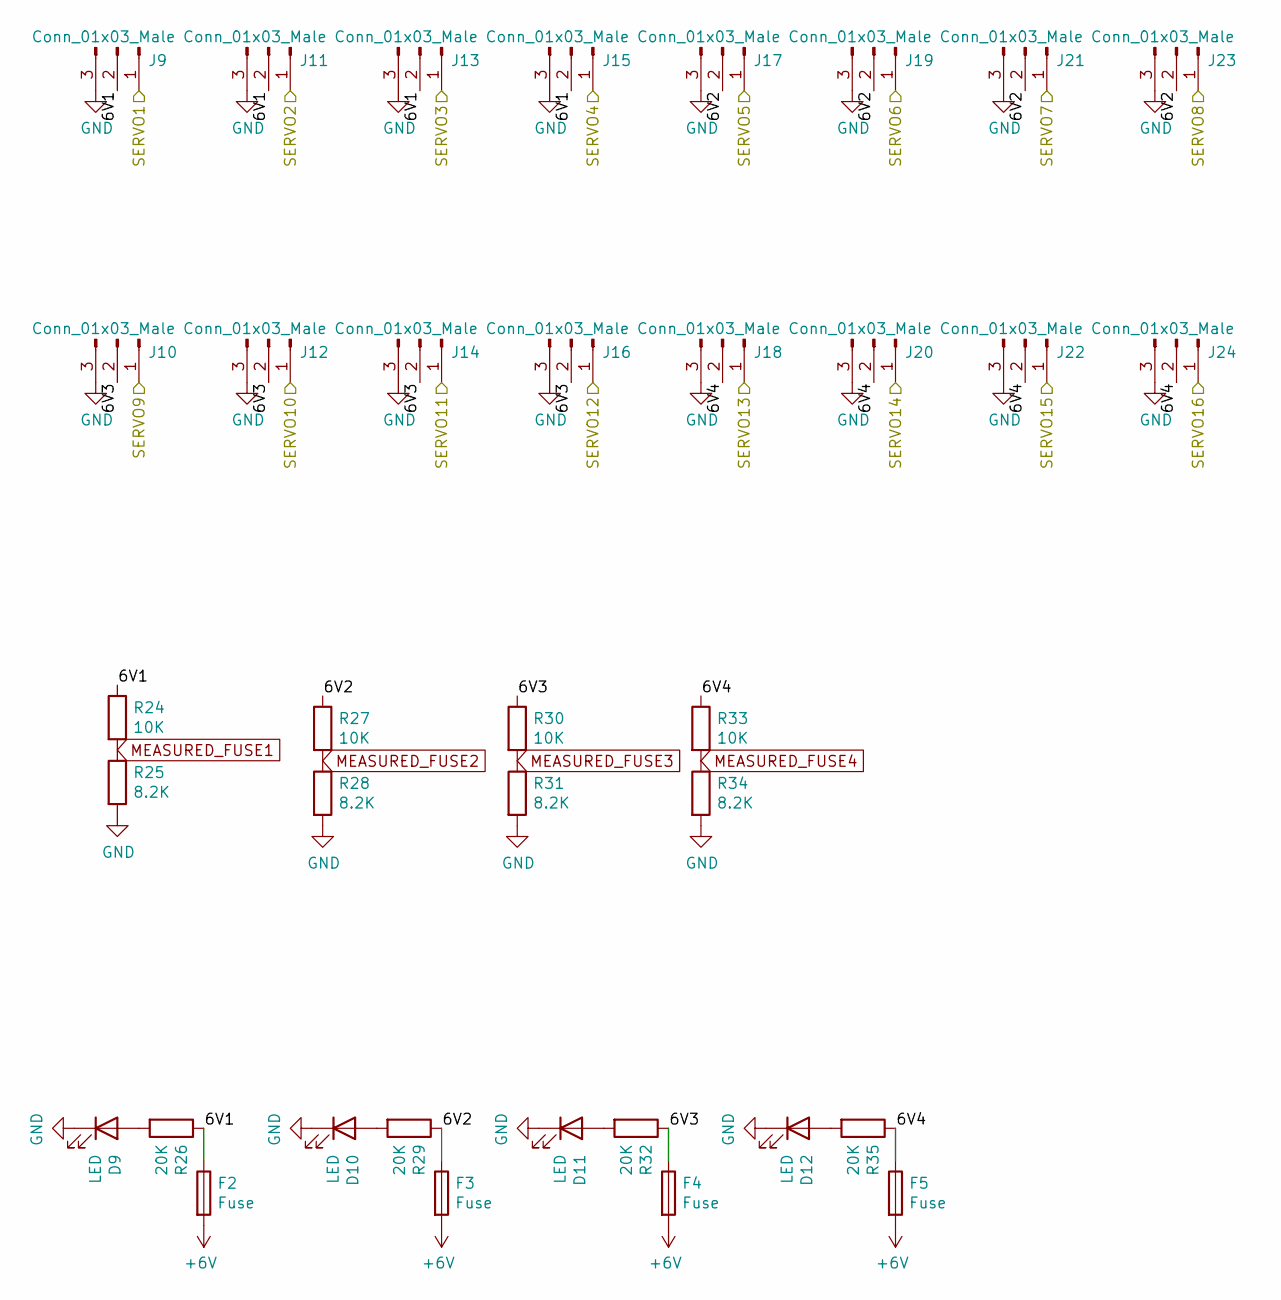
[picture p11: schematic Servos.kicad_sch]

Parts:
D9, D10, D11, D12: LED; LED_0603_1608Metric
F2, F3, F4, F5: Fuse; 0154.250DR
J9, J10, J11, J12, J13, J14, J15, J16, J17, J18, J19, J20, J21, J22, J23, J24: Conn_01x03_Male; PinHeader_1x03_P2.54mm_Vertical
R24, R27, R30, R33: 10K; R_0402_1005Metric
R25, R28, R31, R34: 8.2K; R_0402_1005Metric
R26, R29, R32, R35: 20K; R_0402_1005Metric

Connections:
+6V: F2.2, F3.2, F4.2, F5.2; also elsewhere on the board
/MainBoard/SERVO0: J9.1; also elsewhere on the board
/MainBoard/SERVO1: J11.1; also elsewhere on the board
/MainBoard/SERVO2: J13.1; also elsewhere on the board
/MainBoard/SERVO3: J15.1; also elsewhere on the board
/MainBoard/SERVO4: J17.1; also elsewhere on the board
/MainBoard/SERVO5: J19.1; also elsewhere on the board
/MainBoard/SERVO6: J21.1; also elsewhere on the board
/MainBoard/SERVO7: J23.1; also elsewhere on the board
/MainBoard/SERVO8: J10.1; also elsewhere on the board
/MainBoard/SERVO9: J12.1; also elsewhere on the board
/MainBoard/SERVO10: J14.1; also elsewhere on the board
/MainBoard/SERVO11: J16.1; also elsewhere on the board
/MainBoard/SERVO12: J18.1; also elsewhere on the board
/MainBoard/SERVO13: J20.1; also elsewhere on the board
/MainBoard/SERVO14: J22.1; also elsewhere on the board
/MainBoard/SERVO15: J24.1; also elsewhere on the board
/MainBoard/Servos/6V1: F2.1, J9.2, J11.2, J13.2, J15.2, R24.1, R26.1
/MainBoard/Servos/6V2: F3.1, J17.2, J19.2, J21.2, J23.2, R27.1, R29.1
/MainBoard/Servos/6V3: F4.1, J10.2, J12.2, J14.2, J16.2, R30.1, R32.1
/MainBoard/Servos/6V4: F5.1, J18.2, J20.2, J22.2, J24.2, R33.1, R35.1
GND: D9.1 (K), D10.1 (K), D11.1 (K), D12.1 (K), J9.3, J10.3, J11.3, J12.3, J13.3, J14.3, J15.3, J16.3, J17.3, J18.3, J19.3, J20.3, J21.3, J22.3, J23.3, J24.3, R25.2, R28.2, R31.2, R34.2; also elsewhere on the board
MEASURED_FUSE1: R24.2, R25.1; also elsewhere on the board
MEASURED_FUSE2: R27.2, R28.1; also elsewhere on the board
MEASURED_FUSE3: R30.2, R31.1; also elsewhere on the board
MEASURED_FUSE4: R33.2, R34.1; also elsewhere on the board
unnamed: D9.2 (A), R26.2
unnamed: D10.2 (A), R29.2
unnamed: D11.2 (A), R32.2
unnamed: D12.2 (A), R35.2

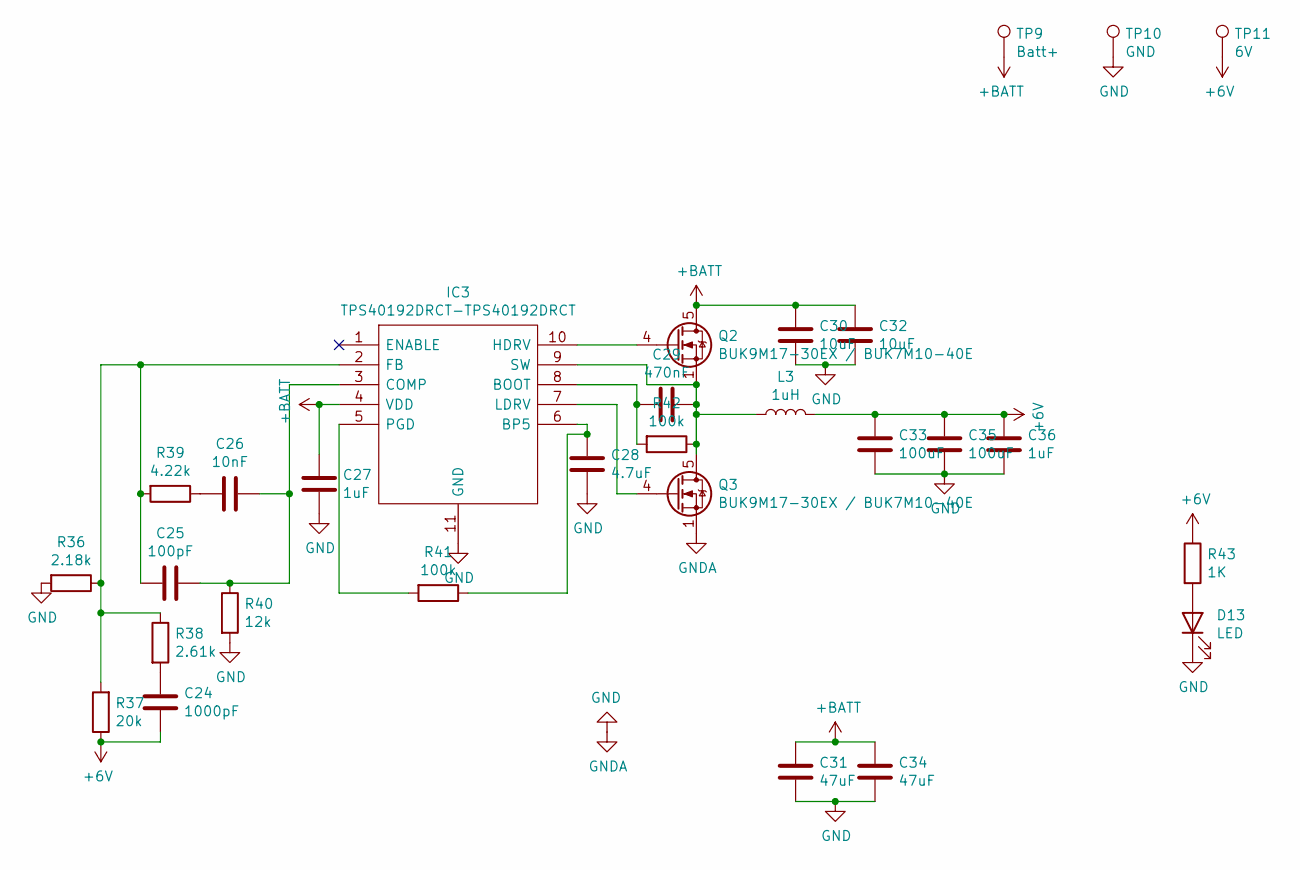
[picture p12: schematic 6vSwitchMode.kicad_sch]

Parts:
C24: 1000pF; C_0402_1005Metric
C25: 100pF; C_0402_1005Metric
C26: 10nF; C_0402_1005Metric
C27, C36: 1uF; C_0402_1005Metric
C28: 4.7uF; C_0402_1005Metric
C29: 470nF; C_0402_1005Metric
C30, C32: 10uF; C_1206_3216Metric
C31, C34: 47uF; C_1206_3216Metric
C33, C35: 100uF; C_1210_3225Metric
D13: LED; LED_0603_1608Metric
IC3: TPS40192DRCT-TPS40192DRCT; VSON-10-1EP_3x3mm_P0.5mm_EP1.2x2mm; Manufacturer_Part_Number TPS40192DRCT; Mouser Part Number 595-TPS40192DRCT
L3: 1uH; L_Bourns_SRP1245A
Q2, Q3: BUK9M17-30EX / BUK7M10-40E; VSON-8_3.3x3.3mm_P0.65mm_NexFET
R36: 2.18k; R_0402_1005Metric
R37: 20k; R_0402_1005Metric
R38: 2.61k; R_0402_1005Metric
R39: 4.22k; R_0402_1005Metric
R40: 12k; R_0402_1005Metric
R41, R42: 100k; R_0402_1005Metric
R43: 1K; R_0402_1005Metric
TP9: Batt+; TestPoint_Pad_D2.0mm
TP10: GND; TestPoint_Pad_D2.0mm
TP11: 6V; TestPoint_Pad_D2.0mm

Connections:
+6V: C24.1, C33.1, C35.1, C36.1, L3.2, R37.1, R43.1, TP11.1; also elsewhere on the board
+BATT: C27.1, C30.1, C31.1, C32.1, C34.1, IC3.4 (VDD), Q2.5 (D), TP9.1; also elsewhere on the board
GND: C27.2, C28.2, C30.2, C31.2, C32.2, C33.2, C34.2, C35.2, C36.2, D13.1 (K), IC3.11 (GND), Q3.1 (S), Q3.2 (S), Q3.3 (S), R36.2, R40.2, TP10.1; also elsewhere on the board
unnamed: C24.2, R38.2
unnamed: C25.1, C26.1, IC3.3 (COMP), R40.1
unnamed: C25.2, IC3.2 (FB), R36.1, R37.2, R38.1, R39.2
unnamed: C26.2, R39.1
unnamed: C28.1, IC3.6 (BP5), R41.1
unnamed: C29.1, IC3.9 (SW), L3.1, Q2.1 (S), Q2.2 (S), Q2.3 (S), Q3.5 (D), R42.1
unnamed: C29.2, IC3.8 (BOOT), R42.2
unnamed: D13.2 (A), R43.2
unnamed: IC3.5 (PGD), R41.2
unnamed: IC3.7 (LDRV), Q3.4 (G)
unnamed: IC3.10 (HDRV), Q2.4 (G)

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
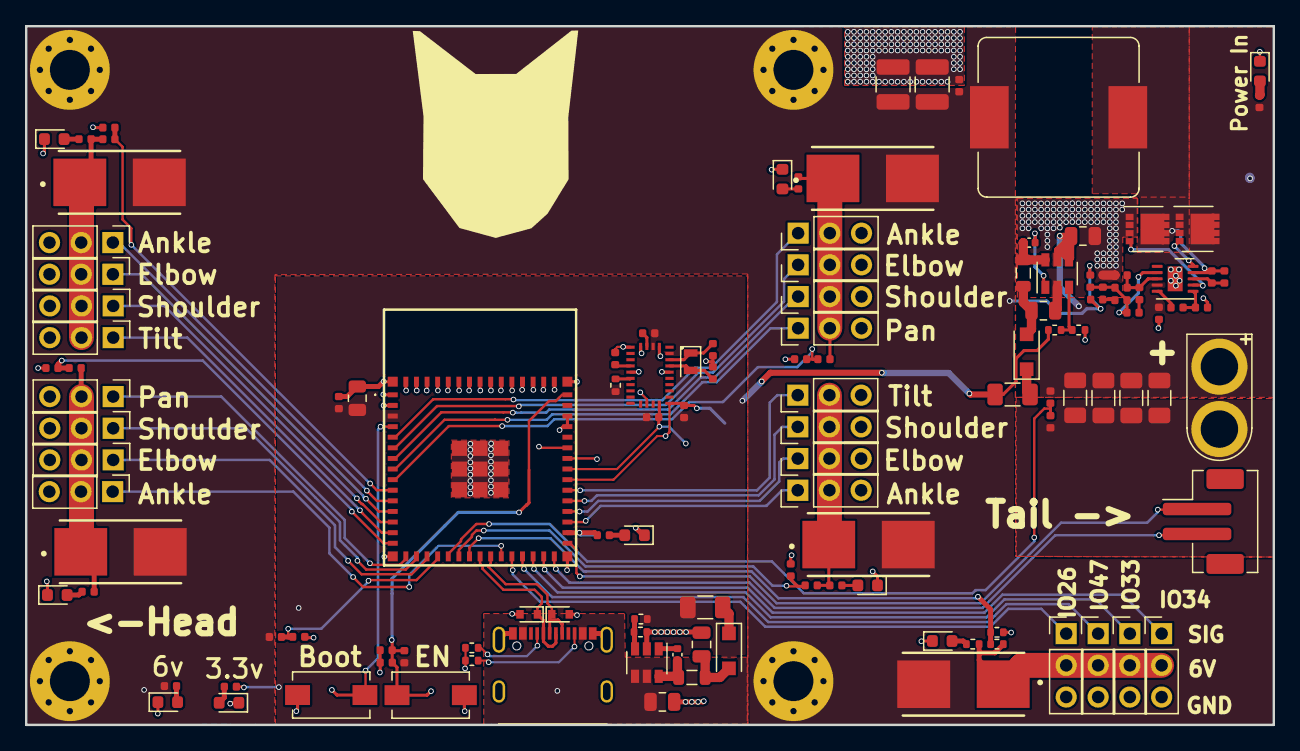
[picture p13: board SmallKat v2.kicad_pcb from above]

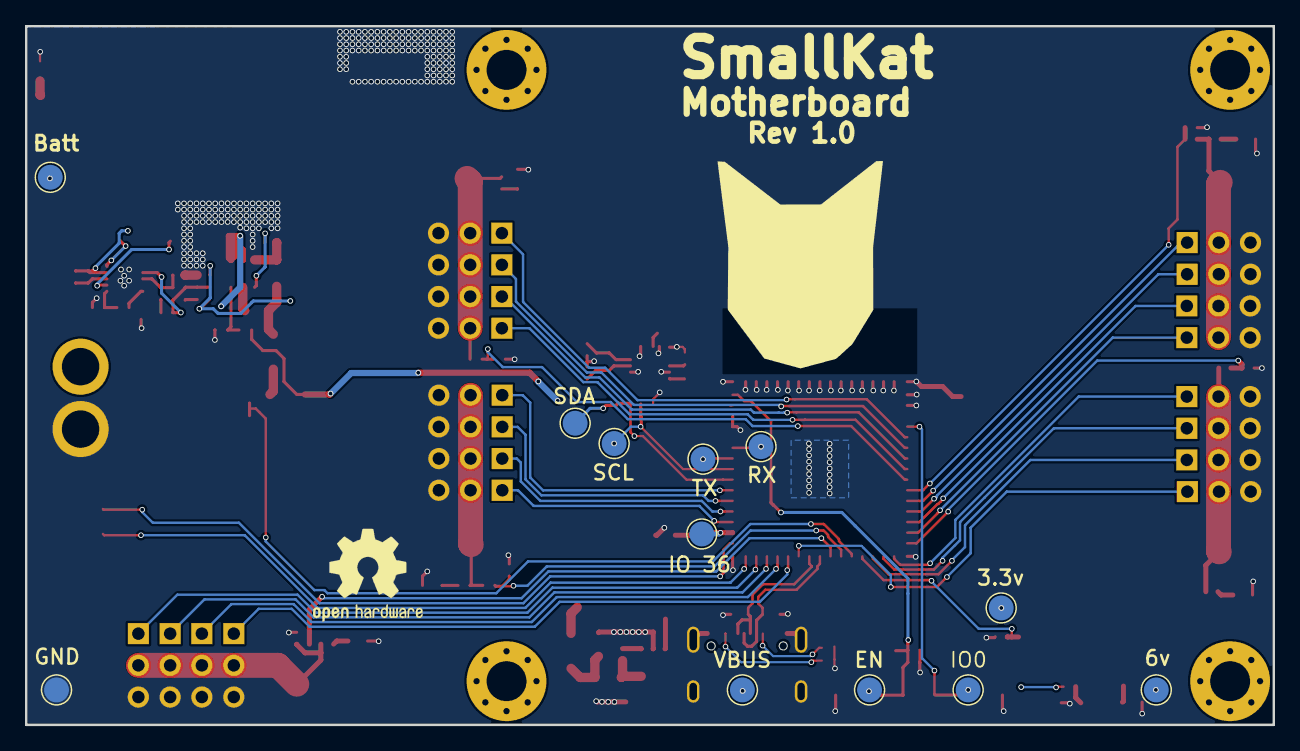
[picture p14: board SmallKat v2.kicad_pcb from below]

Board: 2 copper layers, 100.0 x 56.0 mm, 139 parts (12 on the bottom side), 84 nets.

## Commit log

2019-02-08 First routing rev
    [SmallKat v2.kicad_pcb, SmallKat v2.sch]
2019-02-22 Updated to use BECs and added silkscreen
    [SmallKat v2.kicad_pcb, _saved_SmallKat v2.sch]
2019-04-04 Updated to use nucleo l432kc
    [SmallKat v2.kicad_pcb, SmallKat v2.sch, _saved_SmallKat v2.sch]
2019-11-09 Workign Revision
    [SRP1245A series.stp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]
2019-11-22 In progress of charging implimentation
    [BatteryBalancer.sch, BatteryCharging.sch, BatteryMonitor.sch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]
2019-11-23 Routing done
    [3.sch, 6vSwitchMode.sch, BNO055.sch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]
2020-11-29 This rev removes the safety micro and instead uses the dji battery
    [3.sch, 6vSwitchMode.sch, BNO055.sch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]
2020-12-03 batt connector and all in the right place. has not been ordered, waiting for prev rev to be tested first
    [3.sch, 6vSwitchMode.sch, BNO055.sch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]
2020-12-06 rev, pendingorder
    [1040310811.stp, 3.sch, 6vSwitchMode.sch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]
2020-12-17 rev ordered
    [3.sch, 6vSwitchMode.sch, BNO055.sch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]
2021-01-15 Final order version with all bom files
    [6vSwitchMode.sch, BNO055.sch, Bom_with_components.csv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]
2021-01-23 Ready to order
    [6vSwitchMode.sch, BNO055.sch, ESP32Module.sch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]
2021-03-11 order files
    [2021030415083453977798_新建XLSX工作表.xlsx, BOM.csv, Bom.CSV.csv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]
2021-03-11 ordered version with foot connecotrs
    [3.sch, 6vSwitchMode.sch, BNO055.sch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]
2022-12-31 fully routed, currently 4 layers, ordered 2 layer version with only middle 2 layers removed
    [3.kicad_sch, 6vSwitchMode.kicad_sch, BNO055.kicad_sch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]
2022-12-31 cleaning up old files
    [0154_250dr.psm, 1040310811.stp, 2021030415083453977798_新建XLSX工作表.xlsx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]
2022-12-31 fixing i2c pins to not be on strapping pins
    [ESP32Module.kicad_sch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]
